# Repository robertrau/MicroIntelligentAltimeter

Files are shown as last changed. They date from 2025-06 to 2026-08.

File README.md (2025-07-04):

# MicroIntelligentAltimeter

The Micro Intelligent Altimeter (Mia) flight computer is not designed as a competition altimeter, but as a model rocket altimeter for young people curious to learn more.
That being said, kids can ask the hardest questions, like, how high did my rocket go, or how fast? So, Mia uses an accurate pressure sensor with a comprehensive software package wrapped around it to provide an accurate altitude.

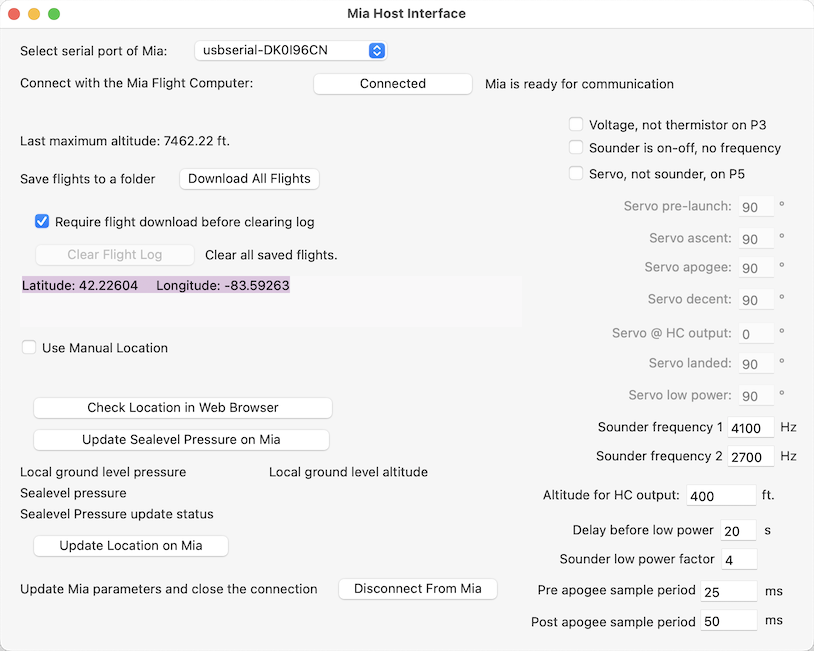
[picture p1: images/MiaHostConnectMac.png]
Picture of Mia's host user interface on a Mac

<p align="center">User Interface on a Mac</p>

<br/><br/>
The board is narrow enough to fit in a BT-5 body tube.

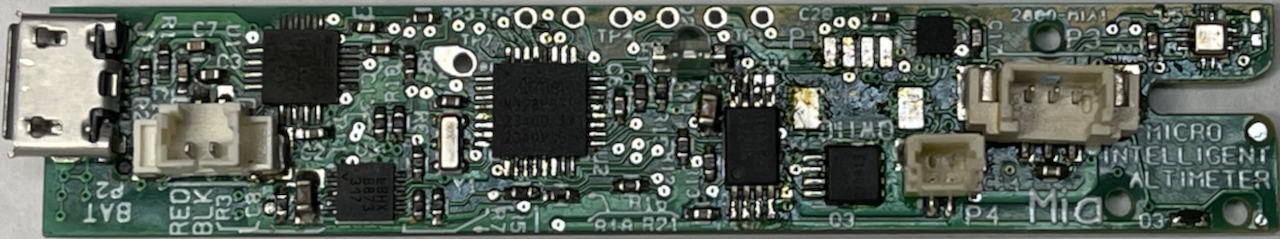
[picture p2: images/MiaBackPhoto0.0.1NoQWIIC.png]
Picture of Mia user interface side

<p align="center">Back of Mia</p>

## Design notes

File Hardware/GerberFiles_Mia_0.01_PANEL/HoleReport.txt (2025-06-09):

Tool   Size   Count  Plated

 T1    0.0550    12     No
 T2    0.0354     6     No
 T3    0.0120   438     Yes
 T4    0.0197     6     Yes
 T5    0.0280    18     Yes
 T6    0.0410     3     Yes

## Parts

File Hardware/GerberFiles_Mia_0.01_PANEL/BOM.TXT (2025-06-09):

1	3	0603-.8x.85	CHG	D2	D2	D2	
2	3	AMPH_10051922-12	OLED	J2	J2	J2	
3	3	ANALOG_DFN10	LTC4063	U3	U3	U3	
4	3	ATMEL_VQFN32	MEGA328	U2	U2	U2	
5	3	BOSCH_BMP390	BMP390	U5	U5	U5	
6	42	C0402R	0.1µF	C1	C11	C12	C13	C14	C15	C17	C18	C19	C2	
					C20	C3	C5	C6	C1	C11	C12	C13	C14	C15	
					C17	C18	C19	C2	C20	C3	C5	C6	C1	C11	
					C12	C13	C14	C15	C17	C18	C19	C2	C20	C3	
					C5	C6	
7	6	C0402R	2.2uF	C10	C9	C10	C9	C10	C9	
8	6	C0402R	33pF	C16	C7	C16	C7	C16	C7	
9	3	C0603R	4.7uF	C4	C4	C4	
10	3	C0805_N	10uF	C8	C8	C8	
11	6	CK_PTS830_S	DISP	SW2	SW4	SW2	SW4	SW2	SW4	
12	3	CK_PTS830_S	RESET	SW3	SW3	SW3	
13	3	CUI_CMT-1102-SMT		PZ1	PZ1	PZ1	
14	6	DFN1006-2	1N4148	D3	D4	D3	D4	D3	D4	
15	3	E_SWITCH_EG1215AA		SW1	SW1	SW1	
16	3	FCI_10118193_S	USB	J1	J1	J1	
17	6	FID40		FID1	FID2	FID1	FID2	FID1	FID2	
18	3	FTDI_WQFN-16	FT230	U1	U1	U1	
19	6	Fiducial_050		U10	U11	U6	U7	U8	U9	
20	3	JST_BM02B	DIGOUT	P4	P4	P4	
21	3	JST_BM04B	QWIIC	P1	P1	P1	
22	3	MEMSIC_12-VFLGA	MC3416	U7	U7	U7	
23	12	MH-NP-0.055		MH1	MH2	MH3	MH4	MH1	MH2	MH3	MH4	MH1	MH2	
					MH3	MH4	
24	3	MOLEX_533984002_S	BAT	P2	P2	P2	
25	3	MOLEX_533984003	ANALOG	P3	P3	P3	
26	3	MOLEX_533984003	EXT BUZ	P5	P5	P5	
27	3	MURATA_CSTNE	8MHz	Y1	Y1	Y1	
28	18	PAD_45.28		TP1	TP2	TP3	TP4	TP5	TP6	TP1	TP2	TP3	TP4	
					TP5	TP6	TP1	TP2	TP3	TP4	TP5	TP6	
29	3	PAD_60.41		TP7	TP7	TP7	
30	3	R0402R	1.00k½	R15	R15	R15	
31	3	R0402R	1.00½	R8	R8	R8	
32	3	R0402R	1.50½	R24	R24	R24	
33	9	R0402R	10.0k½	R14	R17	R6	R14	R17	R6	R14	R17	R6	
34	3	R0402R	100k½	R4	R4	R4	
35	18	R0402R	2.00k½	R12	R13	R16	R22	R23	R9	R12	R13	R16	R22	
					R23	R9	R12	R13	R16	R22	R23	R9	
36	6	R0402R	20.0k½	R18	R5	R18	R5	R18	R5	
37	12	R0402R	21.5k½	R10	R11	R20	R21	R10	R11	R20	R21	R10	R11	
					R20	R21	
38	3	R0402R	274k½	R3	R3	R3	
39	6	R0402R	33.2½	R1	R2	R1	R2	R1	R2	
40	3	R0402R	49.9½	R19	R19	R19	
41	3	R0402_R	0½	R7	R7	R7	
42	3	ROHM_HSMT8	RQ3E180	Q3	Q3	Q3	
43	3	SC-70-6	NL27WZ04	U6	U6	U6	
44	24	TP_CU_50mil		TP10	TP11	TP12	TP13	TP14	TP15	TP8	TP9	TP10	TP11	
					TP12	TP13	TP14	TP15	TP8	TP9	TP10	TP11	TP12	TP13	
					TP14	TP15	TP8	TP9	
45	3	TSSOP-8	CAV24M01	U4	U4	U4	
46	438	VIA-OsmLib		VIA1	VIA100	VIA101	VIA102	VIA103	VIA104	VIA105	VIA106	VIA107	VIA108	
					VIA109	VIA11	VIA110	VIA111	VIA112	VIA113	VIA114	VIA115	VIA116	VIA117	
					VIA118	VIA119	VIA12	VIA120	VIA121	VIA122	VIA123	VIA124	VIA125	VIA126	
					VIA127	VIA128	VIA129	VIA13	VIA130	VIA131	VIA132	VIA133	VIA134	VIA135	
					VIA136	VIA137	VIA138	VIA139	VIA14	VIA140	VIA141	VIA142	VIA143	VIA144	
					VIA145	VIA146	VIA147	VIA148	VIA15	VIA16	VIA17	VIA18	VIA19	VIA2	
					VIA20	VIA21	VIA22	VIA23	VIA24	VIA25	VIA26	VIA27	VIA28	VIA29	
					VIA3	VIA30	VIA32	VIA33	VIA34	VIA35	VIA36	VIA37	VIA38	VIA39	
					VIA4	VIA40	VIA41	VIA42	VIA43	VIA44	VIA45	VIA46	VIA47	VIA48	
					VIA49	VIA5	VIA50	VIA51	VIA52	VIA53	VIA54	VIA55	VIA56	VIA57	
					VIA58	VIA59	VIA6	VIA60	VIA61	VIA62	VIA63	VIA64	VIA65	VIA66	
					VIA67	VIA68	VIA69	VIA7	VIA70	VIA71	VIA72	VIA73	VIA74	VIA75	
					VIA76	VIA77	VIA78	VIA79	VIA8	VIA80	VIA81	VIA82	VIA83	VIA84	
					VIA85	VIA86	VIA87	VIA88	VIA89	VIA9	VIA90	VIA91	VIA92	VIA93	
					VIA94	VIA95	VIA96	VIA97	VIA98	VIA99	VIA1	VIA100	VIA101	VIA102	
					VIA103	VIA104	VIA105	VIA106	VIA107	VIA108	VIA109	VIA11	VIA110	VIA111	
					VIA112	VIA113	VIA114	VIA115	VIA116	VIA117	VIA118	VIA119	VIA12	VIA120	
					VIA121	VIA122	VIA123	VIA124	VIA125	VIA126	VIA127	VIA128	VIA129	VIA13	
					VIA130	VIA131	VIA132	VIA133	VIA134	VIA135	VIA136	VIA137	VIA138	VIA139	
					VIA14	VIA140	VIA141	VIA142	VIA143	VIA144	VIA145	VIA146	VIA147	VIA148	
					VIA15	VIA16	VIA17	VIA18	VIA19	VIA2	VIA20	VIA21	VIA22	VIA23	
					VIA24	VIA25	VIA26	VIA27	VIA28	VIA29	VIA3	VIA30	VIA32	VIA33	
					VIA34	VIA35	VIA36	VIA37	VIA38	VIA39	VIA4	VIA40	VIA41	VIA42	
					VIA43	VIA44	VIA45	VIA46	VIA47	VIA48	VIA49	VIA5	VIA50	VIA51	
					VIA52	VIA53	VIA54	VIA55	VIA56	VIA57	VIA58	VIA59	VIA6	VIA60	
					VIA61	VIA62	VIA63	VIA64	VIA65	VIA66	VIA67	VIA68	VIA69	VIA7	
					VIA70	VIA71	VIA72	VIA73	VIA74	VIA75	VIA76	VIA77	VIA78	VIA79	
					VIA8	VIA80	VIA81	VIA82	VIA83	VIA84	VIA85	VIA86	VIA87	VIA88	
					VIA89	VIA9	VIA90	VIA91	VIA92	VIA93	VIA94	VIA95	VIA96	VIA97	
					VIA98	VIA99	VIA1	VIA100	VIA101	VIA102	VIA103	VIA104	VIA105	VIA106	
					VIA107	VIA108	VIA109	VIA11	VIA110	VIA111	VIA112	VIA113	VIA114	VIA115	
					VIA116	VIA117	VIA118	VIA119	VIA12	VIA120	VIA121	VIA122	VIA123	VIA124	
					VIA125	VIA126	VIA127	VIA128	VIA129	VIA13	VIA130	VIA131	VIA132	VIA133	
					VIA134	VIA135	VIA136	VIA137	VIA138	VIA139	VIA14	VIA140	VIA141	VIA142	
					VIA143	VIA144	VIA145	VIA146	VIA147	VIA148	VIA15	VIA16	VIA17	VIA18	
					VIA19	VIA2	VIA20	VIA21	VIA22	VIA23	VIA24	VIA25	VIA26	VIA27	
					VIA28	VIA29	VIA3	VIA30	VIA32	VIA33	VIA34	VIA35	VIA36	VIA37	
					VIA38	VIA39	VIA4	VIA40	VIA41	VIA42	VIA43	VIA44	VIA45	VIA46	
					VIA47	VIA48	VIA49	VIA5	VIA50	VIA51	VIA52	VIA53	VIA54	VIA55	
					VIA56	VIA57	VIA58	VIA59	VIA6	VIA60	VIA61	VIA62	VIA63	VIA64	
					VIA65	VIA66	VIA67	VIA68	VIA69	VIA7	VIA70	VIA71	VIA72	VIA73	
					VIA74	VIA75	VIA76	VIA77	VIA78	VIA79	VIA8	VIA80	VIA81	VIA82	
					VIA83	VIA84	VIA85	VIA86	VIA87	VIA88	VIA89	VIA9	VIA90	VIA91	
					VIA92	VIA93	VIA94	VIA95	VIA96	VIA97	VIA98	VIA99	
47	3	VISHAY_VEMT2	VEMT2523SLX01	Q2	Q2	Q2

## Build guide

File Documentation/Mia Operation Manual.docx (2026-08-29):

Mia

Micro Intelligent Altimeter

A Rocket Sensor Platform for Learning

Arduino Compatible

Pressure Altimeter

Thermometer

Accelerometer

Revision 0.06

7/23/2025

Read this entire manual

Introduction

Congratulations, you have just ~~purchased~~, er, bought the parts, soldered, loaded a bootloader, and programmed a Mia flight computer!

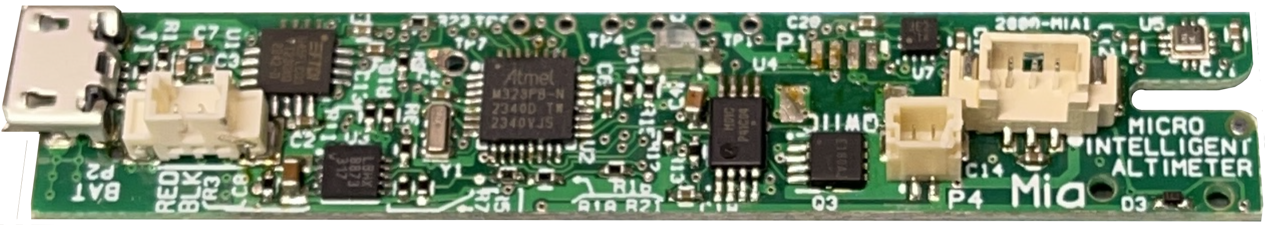
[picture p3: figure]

The Mia flight computer is not designed as a competition altimeter, but as a model rocket altimeter for young people curious to learn more.

That being said, kids can ask the hardest questions, like, how high did my rocket go, or how fast? So, Mia uses an accurate pressure sensor with a comprehensive software package wrapped around it to provide an accurate altitude when needed. You can review the accuracy specifications in the BMP581 data sheet.

In its simplest form, you can turn on your Mia, pop it into a rocket, launch, and recover it, and read your peak altitude on the OLED display. Then do it all over again. No mobile device or computer required. A tiny 30mAh LiPo cell with last for hours of flying. Without worrying about setting the sea level pressure, your reported altitudes may be a little shifted, but they will be accurate relative to one another. You can count on the Mia to find the winner in a friendly altitude competition.

If you require an accurate altitude, using only the buttons and OLED display, you can set the sea level pressure or field altitude for your location. This will likely require a mobile device to retrieve this data from a weather site, GPS, or mobile application. If you have a Windows/Mac/Linux/Raspberry Pi computer with internet access, you can use the Mia host application to set sea level, as well as other features. With an accurate sea level pressure set your reported altitude will be very accurate. See Appendix A for details on how an accurate sea level pressure, or field altitude, is required to provide an accurate altitude.

More advanced flyers, using the host computer application, with internet access, can do:

1. Set sea level pressure (automatic with internet connection and nearby national weather service measurement)
2. Set time (automatic with internet connection)
3. Location (automatic with internet connection)
4. Downloading and clearing of flight log data
5. Set the altitude for the high current output to turn on during descent.
6. Configure low power options
7. Configure Mia for what is connected to connector P3 (thermistor, or a sensor with voltage output)
8. Configure Mia for what is connected to connector P5 (sounder or servo)

Then the Mia can be flown, and after recovery, a flight log can be downloaded with the host application and the flight log can be viewed in a spread sheet. If the user prefers to use a terminal emulator, all parameters and downloads can be performed with the command interface.

For those with an interest in programming, all the flight firmware and host computer software are available as open-source software. The flight firmware is developed in the free Arduino IDE. The code is heavily commented to help those wanting to change, experiment, or just learn from the code. The host application is developed in the low cost XOJO IDE (free for targeting only the Raspberry Pi).

Description

The Mia is a small formfactor sensor platform with embedded software designed for young people interested in rockets, science, technology, engineering, or who are just looking for a challenge.

The Mia includes:

1. An Arduino based architecture providing an accessible and well supported development environment.
2. A power supply that allows operation from a battery, or USB power with a battery attached.
3. USB to serial bridge for communicating with the MCU with the Arduino environment
4. An OLED display as a user interface
5. Three buttons as part of the user interface.
6. Pressure sensor for altitude.
7. A three-axis accelerometer.
8. Light sensor.
9. A connector, P3, that can monitor an external thermistor or any other voltage-output sensor
10. A high current output that switches to ground.
11. QWIIC connector for sensor expansion.
12. Either a soldered-on sounder or a connector, P5, for either a sounder or servo.
13. A 2-megabit flight log EEPROM. This stores 8 thousand flight records.
14. The MCU is a Microchip ATMEGA328PB with 32kB of FLASH memory running at 8MHz.

The flight firmware includes:

1. Flight mode displays maximum altitude after rockets lands.
2. Accurate altitude settings can be entered without a mobile device or computer.
3. Can set sea level/field altitude
4. Can set altitude for high current output to trigger

Basic Operation

For the most simple and fun applications, the Mia offers modest accuracy maximum altitude (apogee) reporting without any other equipment. For reliable and long-lasting performance, some care and preparation are required.

1. The Mia can be damaged by rocket motor ejection charge gases. The Mia must be used in a payload section of a rocket and never put in with the parachute or streamer. Also check that your payload barrier between the payload section and the parachute compartment is airtight. Some plastic adapters have openings where ejection gases can pass into the payload section.
2. The Mia battery must be supported so the wires can’t be stressed during launch or ejection. It is a good idea to use double sticky foam tape to mount the battery to the Mia.
3. If your Mia is built without certain parts and flown as a bare PCB assembly, your Mia can fit in a body tube as small as a BT-5. The battery must be below the Mia in this small of a body tube. Make sure that the battery wires will not be stressed. See Appendix C for build requirements for BT-5 applications.
4. Remember to make it easy to get your Mia out of its payload section so you can read the maximum altitude.
5. Many payload sections are simply friction fit together. Even though the Mia weights about 5 grams, during ejection it can overcome the friction holding a payload section together and fall out hundreds of feet in the air. Use tape to hold a payload section together so you don’t lose your Mia.
6. Using a pressure sensor to measure altitude requires your payload to be at the pressure around your rocket. You must have a small hole from your payload section to the outside to get an accurate altitude. Do not put the hole in your nose cone or you will get an incorrect pressure.
7. After you have installed you Mia in its payload section it is a good idea to use an easy-to-remove tape (such as blue painter’s tape) over the air hole so wind blowing over the hole won’t trigger a launch detect.
8. If you want to use the light sensor as a spin rate sensor you must have a hole in your payload section or a clear payload section for the light to enter. This hole can also serve as the air pressure entry if the hole location is located far enough back for a real pressure reading.

Intermediate Operation

For applications where you want accurate altitude and to use the high current output, you can use the buttons and display on the Mia. No host computer is needed but you will need to set the sea level pressure to get an accurate altitude.

Advanced Operation

For applications where you want to change how the Mia behaves you can use the Mia Host application. It runs on Windows, Mac, x86 Linux, and the Raspberry Pi.

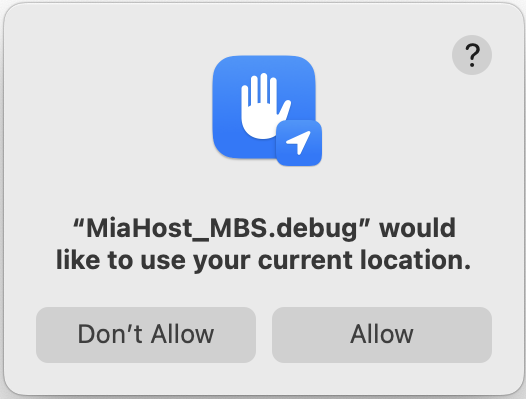
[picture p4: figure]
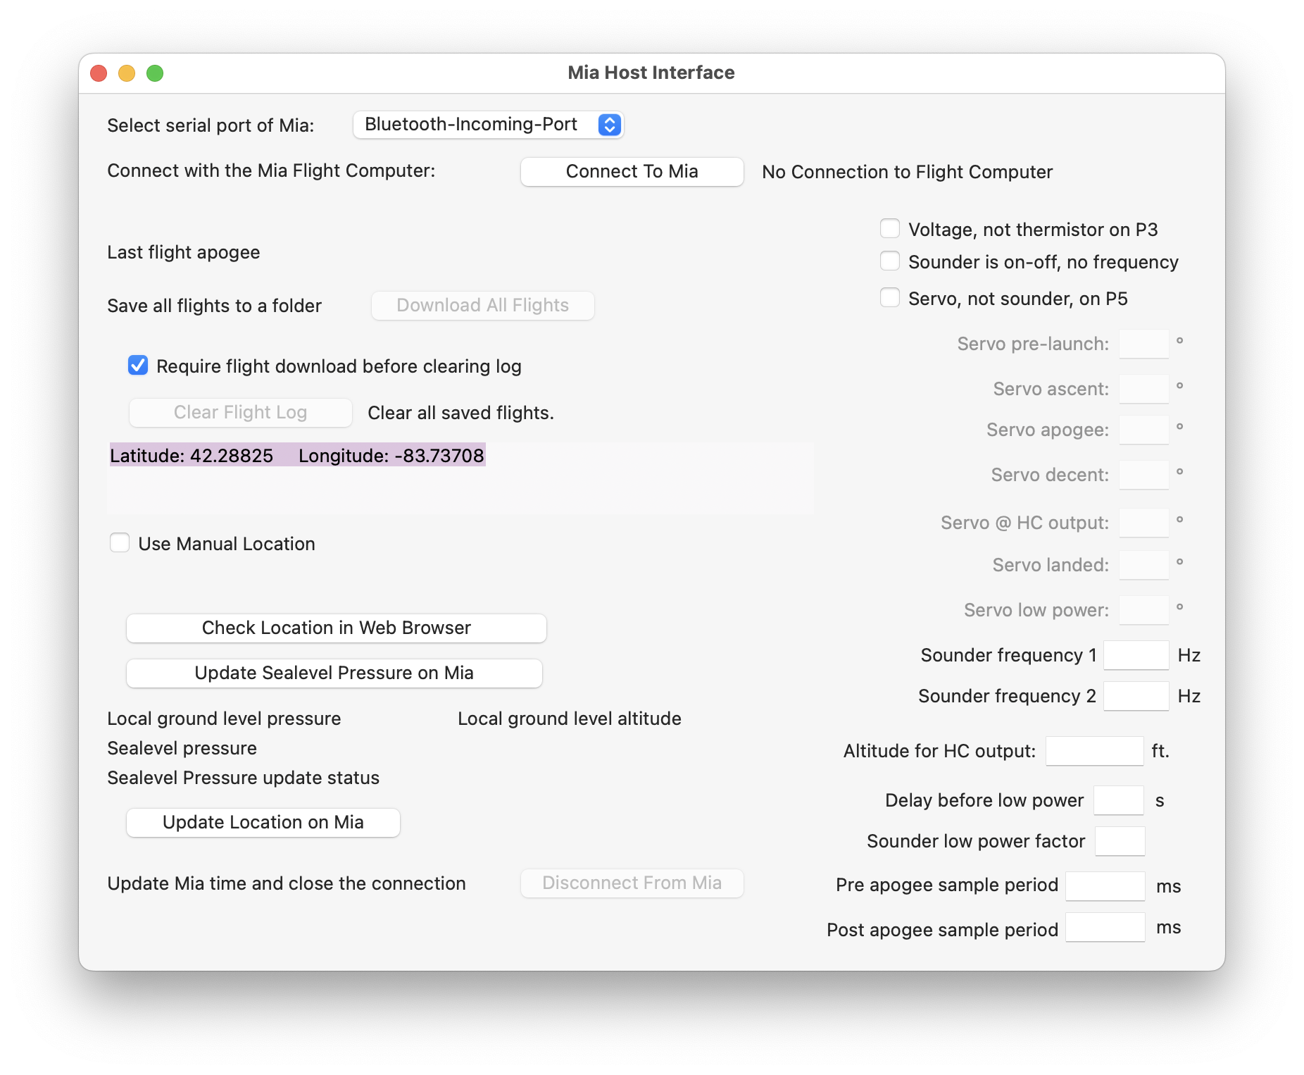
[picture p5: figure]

The left side of the Mia Host window is where you establish your connection with your Mia, download your flight logs, update your sea level pressure, location, and time.

The right side of the Mia Host window allows some advanced user configuration features.

Most of these features requires external hardware connections to the Mia. The options for low power operation do not require any additional connections or hardware.

Voltage, not thermistor on P3

The user can plug a muRata NXFT15XH103FEAB050 thermistor into P3, or any other voltage output sensor. If the thermistor is used the Mia does the conversion from resistance to temperature. If another sensor is used, the Mia will record the voltage on P3. Check the box if you are using a voltage output sensor.

Sounder is on-off, no frequency

Servo Pre-launch

The servo position while waiting for lift off. Set to a value from 0 to 180.

Servo Ascent

The servo will move to this position at launch detect. It will stay at this position through the ascent. Set to a value from 0 to 180.

Servo Apogee

At apogee the servo will move tto this position. Then, after 0.40 seconds, the servo will move to the descent position. Set to a value from 0 to 180.

Servo Descent

The servo will move to the descent position after the 0.40 second long Apogee position. It will stay at this position until the altitude set for the high current output. Then it moves to the 'Servo @ HC output' position. Set to a value from 0 to 180.

Servo @ HC Output

The servo will move to this position at the altitude set for the high current output to turn on. It will stay at this position through landing. Set to a value from 0 to 180.

Servo Landed

After detecting landing the servo moves to this position. It stays here for the duration of the 'Delay before low power' timer, then the servo will move to its last position, the low power position. Set to a value from 0 to 180.

Servo Low-Power

After the flight is complete and the delay before low power time has passed the servo moves to this final position. Set to a value from 0 to 180.

Altitude for high current output

Set the altitude that this output turns on during descent.

The high current output on connector P4 can sink up to 1 amp of current if wired with 28AWG wiring. The MOSFET switch to ground is a high current device with a ‘on’ resistance of 6 milliohms. The connector is rated at 1.0 amp so only use low current devices.

Programming the Mia for custom requirements

The source code is well commented with hundreds of lines of details and explanation. There are also notes specifically for programmers and software engineers who want to modify the Mia software.

If you are a developer, here is some helpful information

Source code conventions:

We use the prefix N_ for active low digital pins.

Part way through the project we started adding a units suffix to variables to reduce unit confusion.

Unused MCU pins must be either an output or an input with a pull up or down so the pins don't float and draw excess current.

Programmer tips:

1) This software keeps track of approximate date and time. This helps keep flight logs in order. Please keep the #define BIRTH_TIME_OF_THIS_VERSION up to date with every build.

2) If you are adding software to Mia and need more FLASH space, you can:

A) Reduce or eliminate the instructions in DisplayInstructions() function. (Just comment out the call 'DisplayInstructions();', the linker will dead strip.)

B) Reduce or eliminate DoSplashScreen() function.

C) Reduce or eliminate DoSensorDisplayLoop() function as this is only used for diagnostics.

D) Reduce or eliminate the temperature look up table (about 412 bytes) and convert temperature differently, or not at all.

E) Remove auto-configuration support for the old Mia 0.0.0

F) Remove Buzzer function if not used.

G) Remove servo support if not used.

H) Revert to the standard ATMEGA328 Variant. You loose access to D23-D26 which may not matter but this saves a few hundred bytes.

I) Remove the host mode help command.

J) If a buzzer on-off pattern is not required, you can eliminate the DoBuzzer() function.

3) Internaal EEPROM addresses 232 and up are unused.

4) Test Point 7 has a hole on the board large enough to easily solder to, it is connected to D3. It is currently unused and available for any purpose.

5) Many different sensors, Memory, controllers are available with a QWIIC connector that can be used with the Mia.

Appendix A

Details of using air pressure to find altitude.

Air pressure is a good indication of altitude and has been used for that purpose for aircraft from 1928 to the present. That being said, it is not an absolute solution, it still needs a reference pressure. Aircraft altimeters allow you to dial in a pressure with a knob on the side of the dial. This is an important step in the pre-flight checklist for any aircraft pilot. This step is also an important step for you with the Mia.

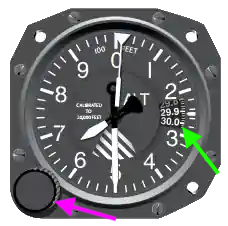
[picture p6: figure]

Figure 2345

To understand what is going on with air pressure you need to understand that air is compressible. As a comparison, water is not compressible. This makes the math very different for finding your depth in water verses finding your height in the air.

Imagin you are 100 feet under water and you want to rise to 50 feet under water. This is similar to a stack of 100 glass marbles in a tube. Half the pressure will be half the marbles, and half the marbles will be 50 feet up, easy.

Now, lets say you are on the surface of the land and you want to go up 50 feet. This time we are in compressible air. Imagine now that you have a tube filled with soft foam balls instead of marbles. At the top your balls are still round, but at the bottom you have a squished nearly flat foam ball from the weight of the other balls. This time you count up 50 foam balls and you are no where near half way.

This is further complicated by the fact that just like the ocean has waves, our atmosphere has waves, we call them high pressure regions.

More can be learned at these links:

https://www.engineeringtoolbox.com/air-altitude-pressure-d_462.html

https://en.wikipedia.org/wiki/Atmospheric_pressure

Earth’s daily pressure changes:

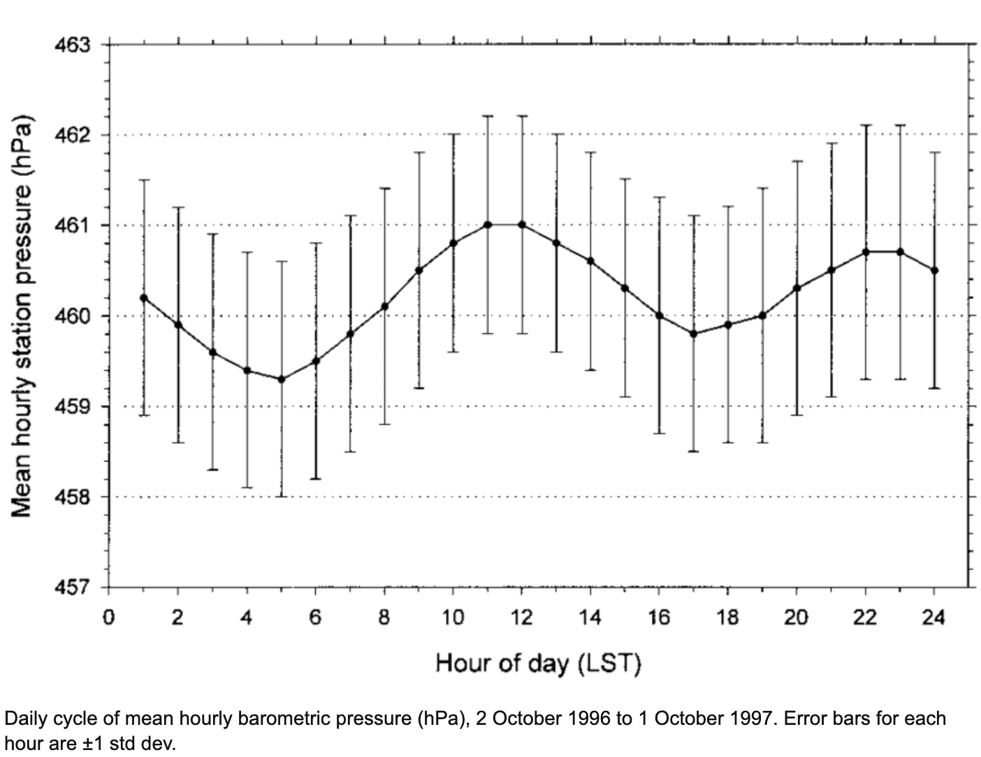
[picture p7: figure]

Here is a collection of high and low pressure extremes on earth on May 13, 2026.

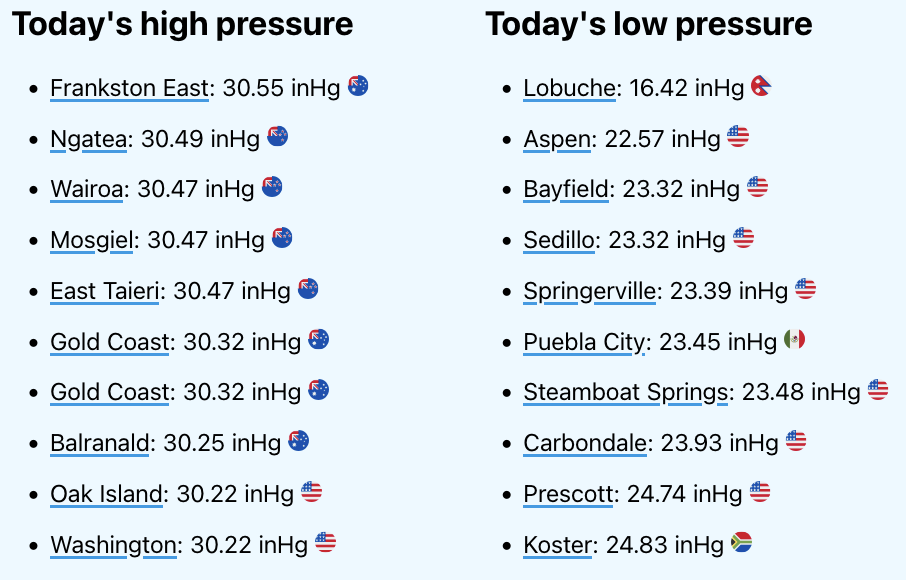
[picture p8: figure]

An example of reported altitudes with and without sea level pressure correction.

For a city with an elevation of 191 meters, Ypsilanti, MI

For a day with a pressure of 15.0 mb below normal

Using uncertainty of a BMP581 sensor,

Apogee altitude above sea level with sea level correction is between 1640.85 meters, and 1641.15 meters.

Apogee altitude above sea level without sea level correction is between 1761.82 meters, and 1762.12 meters.

With sea level correction altitude will be reported between 1449.85 and 1450.15

Without sea level correction altitude will be reported between 1445.74 and 1446.04

Appendix B

Example science projects using the Mia

Compare altitude measure methods by integrating acceleration vs. air pressure.

Upper atmospheric air sample mission using a servo.

Rocket spin rate and its effect on maximum altitude using the light sensor and different fin angles.

The effect of microgravity on light interfering solutions using the light sensor and accelerometer.

Appendix C

Requirements and recommendations for using the Mia in BT-5 body tubes.

The Mia PCB is 12.8mm wide. By itself this easily fits in a BT-5. If the Mia is assembled with optional certain components, it will not fit in a BT-5. These are detailed below:

1. Connector P5 must not be installed, or it will directly interfere with a BT-5
2. Connector P1 must not be used. P1 doesn’t interfere with a BT-5 but the mating connector will interfere with a BT-5
3. The OLED display must be attached with 1.5mm thick double sided foam tape. Any thicker and the OLED will interfere with a BT-5
4. The battery will not fit along side of the Mia, it must be place above or below the Mia. The Mia and battery must be mounted so the battery wires are not stressed.
5. BT-5 diameter rockets limit you to small rocket motors. This may make you want to remove all the unnecessary mass you can. The Mia will operate as an altimeter without the following components:

Connectors: P1, P3, P4, and P5. Other components: Q2 (light sensor), Q3 (High current sensor).

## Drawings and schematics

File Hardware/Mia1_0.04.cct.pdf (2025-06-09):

A | A
B | B
C | C
D | D
E | E
F | F
G | G
H | H
I | I Date:
Document Number: | Rev:

## Sheet:

## TITLE:

Rev. 0.00 Prototype release
Rev. 0.01 Added SW4 and CHG signal to MCU inputs. Added series resistors on TX & RX lines between LTC4063 & FT230 power domains.
Added accelerometer. Changed battery charge resistor values. Added capacitance on Plus3.0V. Board narrowed by 0.2mm. Added USB ESD capacitors.
Rev. 0.02 Layout improvment. PCB part number added as "MIA1-0.02"
Rev. 0.03 Layout improvment around accelerometer, improved grounding. PCB PN reduced to version only "0.03"
Rev. 0.04 Changed BMP390 to a BMP581. Changed U4 to a 2Mb ST M24M02E. No layout change.

PCB Assembly mass: &GmMassTot grams

Copyright 2024-2025, all rights reserved

Design Revision: 0.01 | Drawing Revision: H

PCB Fabrication Notes:
1) Each board in the panel must have a unique number, in
copper, to track which part of the panel each board came from.
2) The solder mask must be green.
3) Solder side silkscreen must be must.
4) Component side silkscreen must be white.

Component Hole Count: 8

# FINISHED

SMT pad Count: 496

Board width: 12.8 mm

Board length: 65.5 mm
Modified: 5/9/25 5:07 PM

Created: 4/21/25 8:46 PM

## Small Rocket Computer

File: Mia1_0.04.cct | 2000-MIA1-0.01

Printed: 5/9/25 5:07 PM

Component side area used is 456 mm^2, or 53% of 851.5 mm^2

Cost of Assembly: &CostTotalAsy

Warning Count: 74

Operating temperature range: 0° C to 70°C &NoteTempWavr

Error Count: 0

Package count solder side: 23

Package count component side: 53

Net List File Name: Mia1_0.04.txt

At a quantity of: 10

Parts Cost: $40.1189

Designer: Robert & Rich Rau

Solder side area used is 490 mm^2, or 57% of 851.5 mm^2

Custom attributes:

fill in different build attributes

Last Used Devices:
C20
D4
FID2
HW1
J2
MH4
P5
PCB7
PZ1
Q3
R24
SW4
TP15
U7

PCB Layout Notes:
1) Test points accessable from bottom.
2) OLED & switches on same side of board.
3) Add vias on SMT connector machanical pads.

# 2000-MIA1-0.01

Attach OLED to J2

Bottom side SMT

Assembly Step 3

Assembly Step 2

Assembly Step 1

Top side SMT

Unused Units:

Top Side Documentation | Bottom Side Documentation

Silkscreen: Mia

FID1

Fiducial,40mil,Top/Bot side

FID2

Fiducial,40mil,Top/Bot side

Printed Circuit Board:
In Copper:

Printed circuit board, FR4, 1.0mm thick, 2 Layer

1700-MIA1-0.03

PCB NOTE:
All nets that start with KS are "Keep Short" nets. They are grouped at the top of the netlist. PCB5

PCB NOTE:
All connector silkscreen RefDes must be 3mm high on both sides of the board where possible. PCB6

MH1

MH-NP-0.055

MH2

Silkscreen: | MICRO INTELLIGENT ALTIMETER
Silkscreen: | BOARD: PRO MINI
Silkscreen: | PROC: ATMEGA328P 3.3V
MH3 | MH4

B | B
2000-MIA1-0.01 | FINISHED

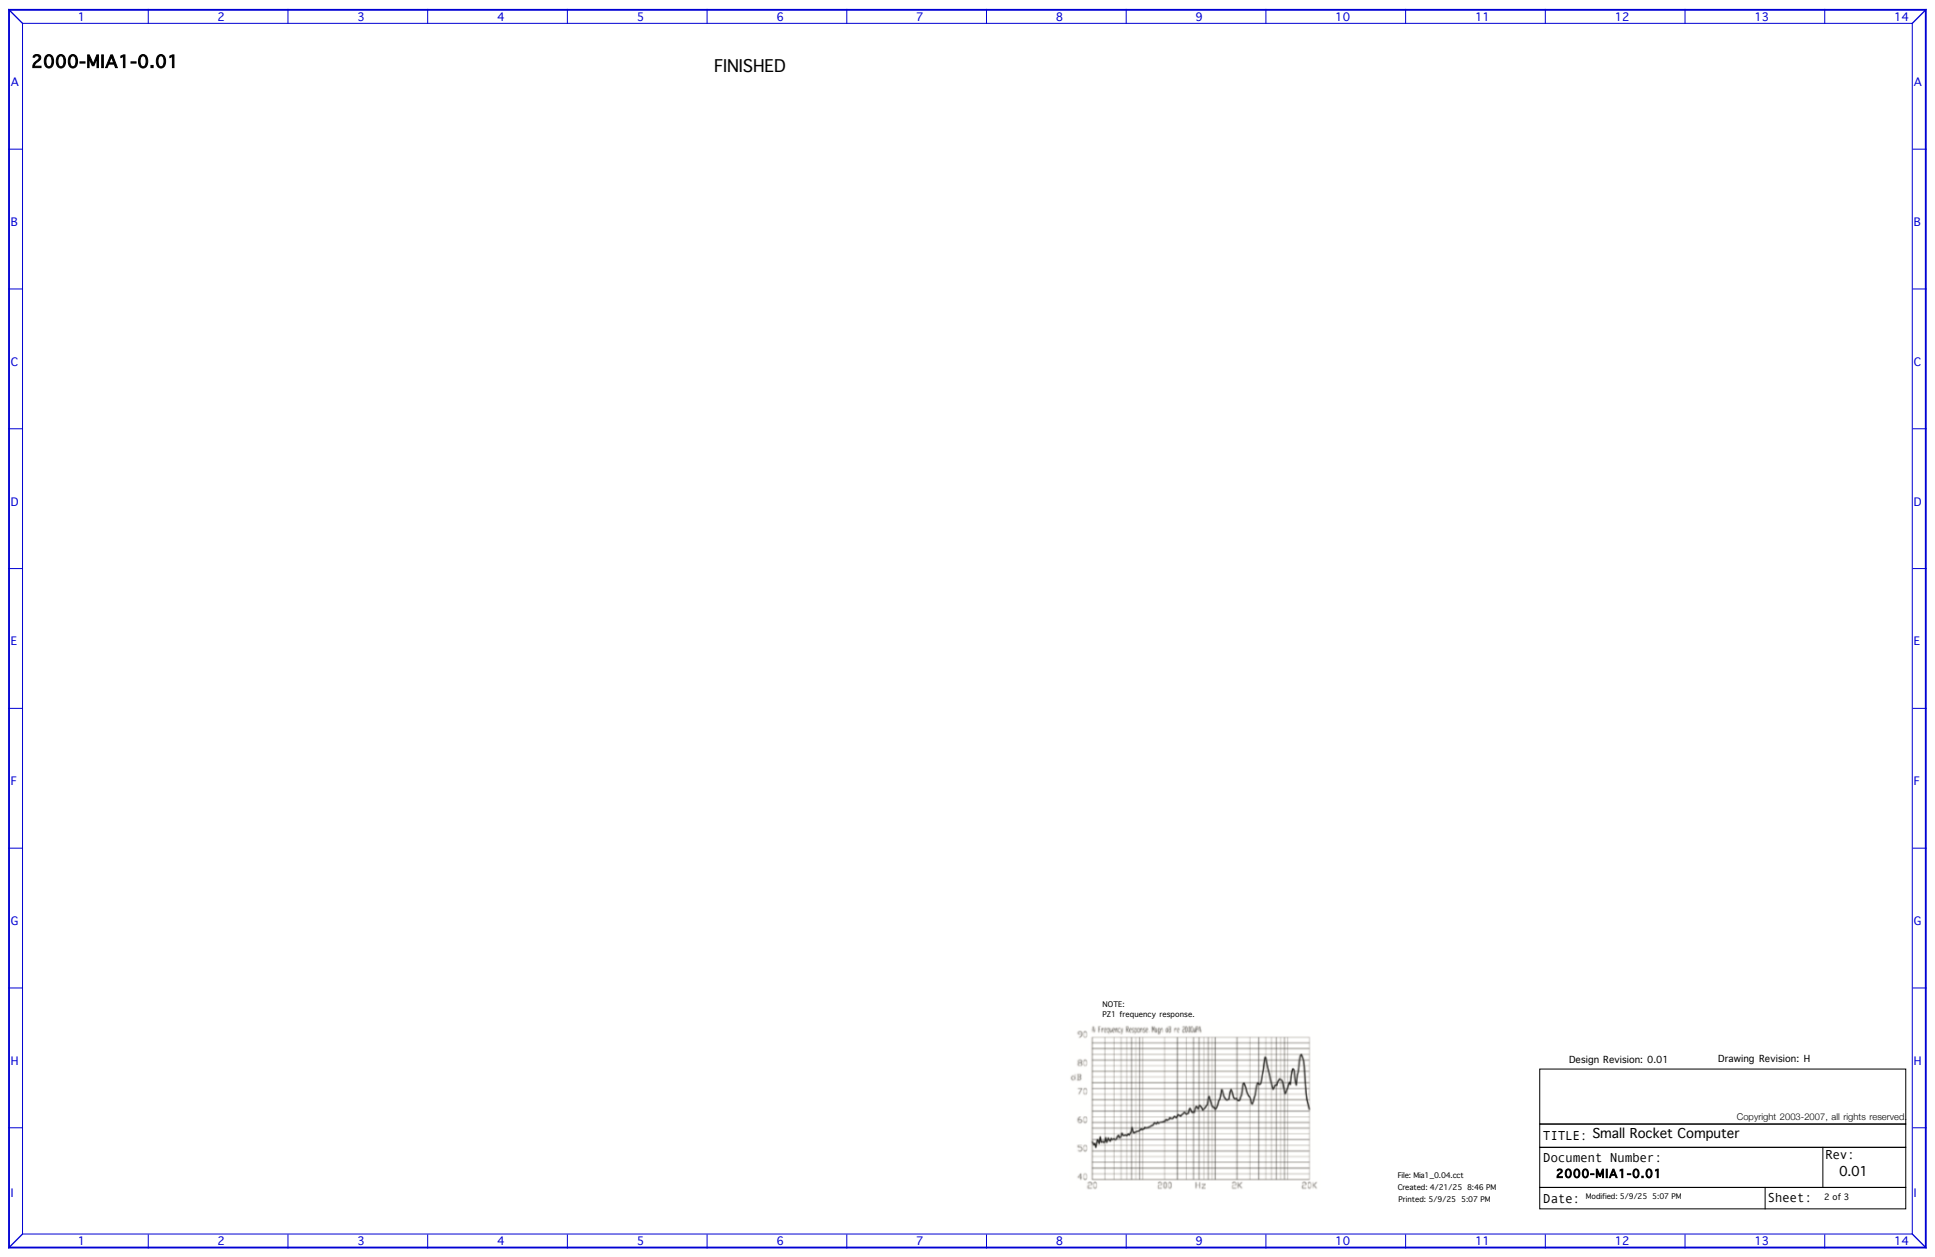
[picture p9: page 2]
I Date:; Document Number:; Rev:; TITLE:; NOTE: PZ1 frequency response.; Design Revision: 0.01; Drawing Revision: H; File: Mia1_0.04.cct; 2000-MIA1-0.01

Copyright 2003-2007, all rights reserved.

Small Rocket Computer

B | B

# FINISHED

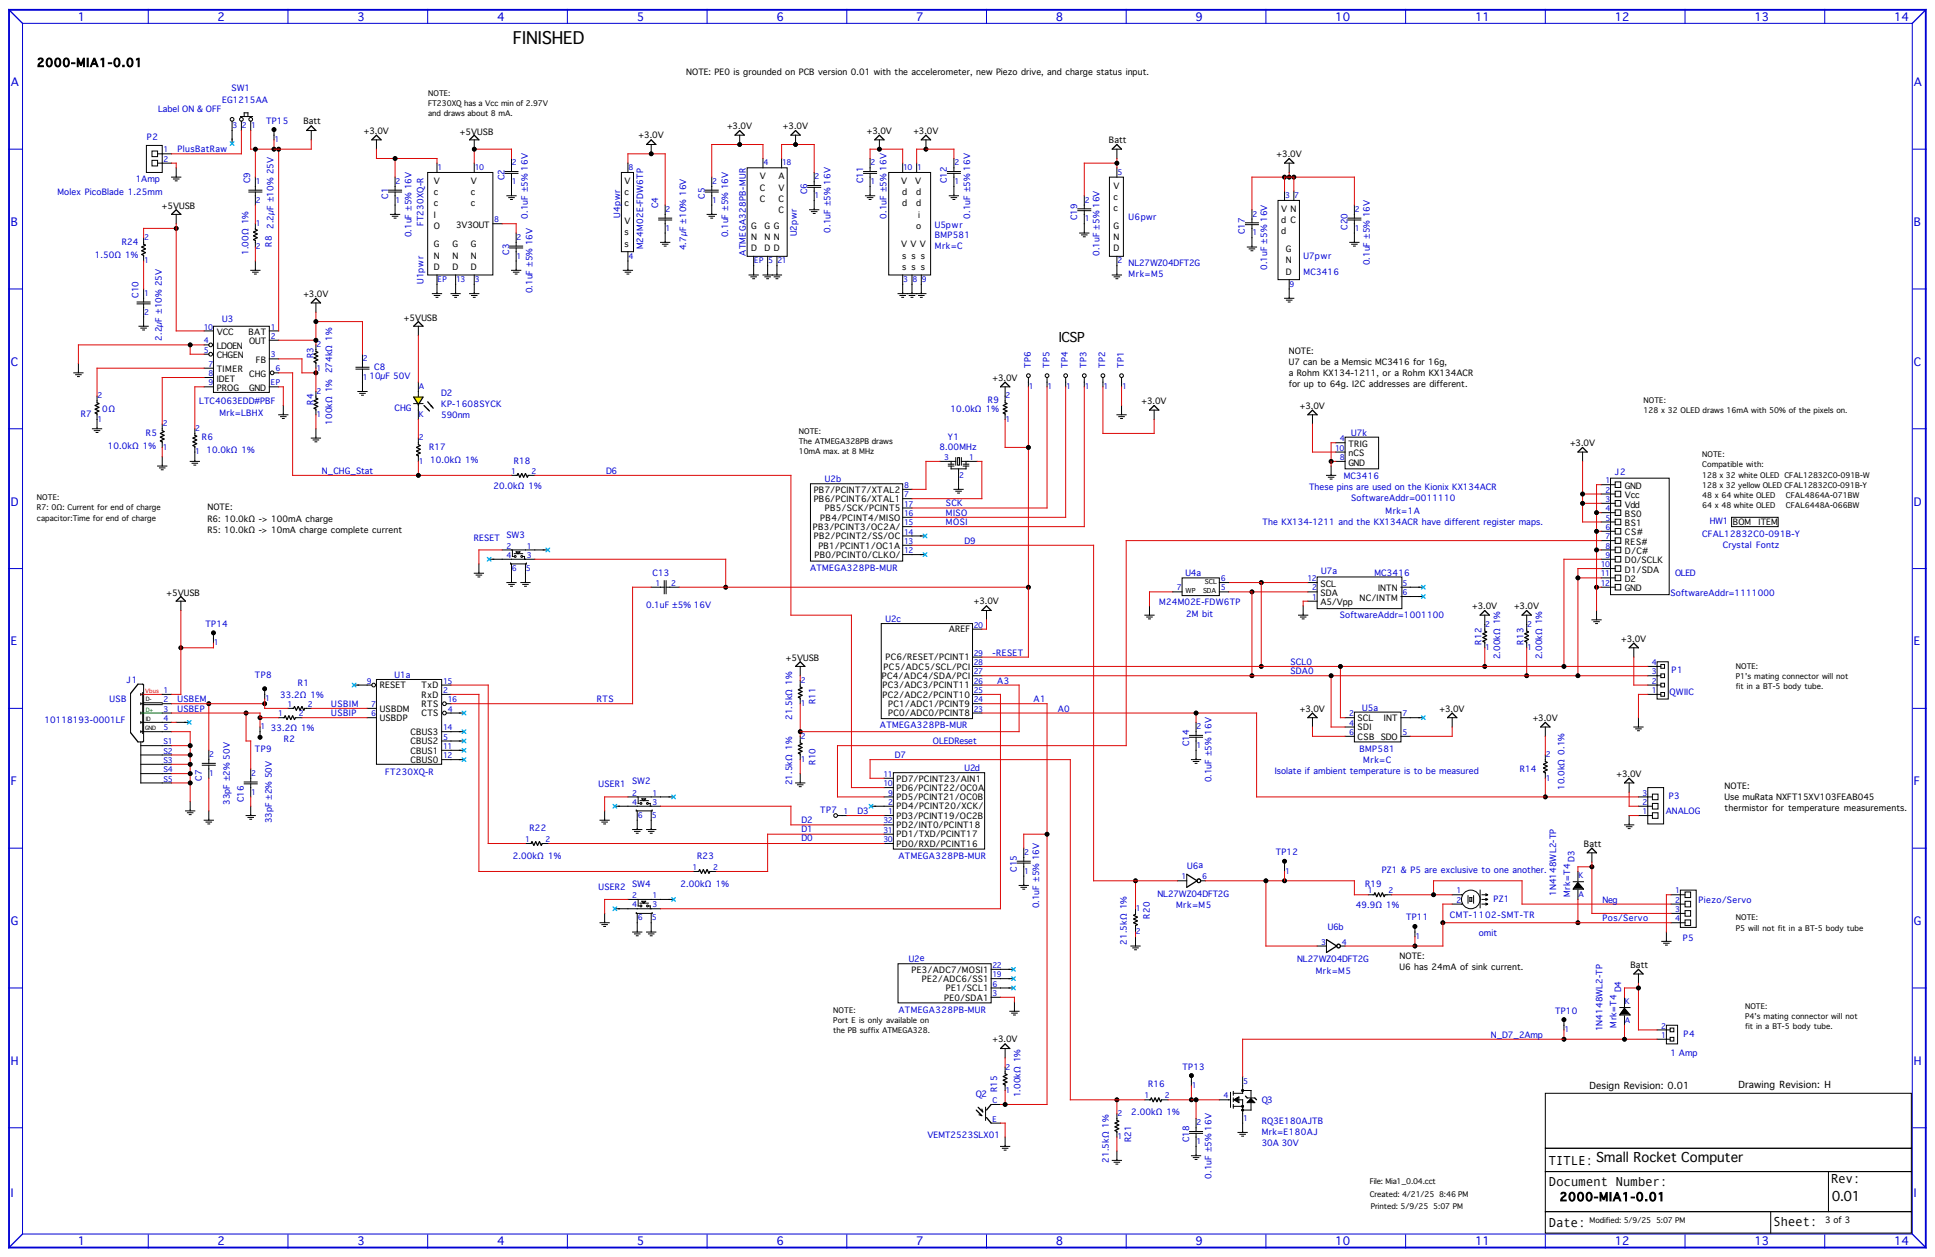
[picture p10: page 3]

NOTE: PE0 is grounded on PCB version 0.01 with the accelerometer, new Piezo drive, and charge status input.

NOTE:
FT230XQ has a Vcc min of 2.97V
and draws about 8 mA.

U7 can be a Memsic MC3416 for 16g,
a Rohm KX134-1211, or a Rohm KX134ACR
for up to 64g. I2C addresses are different.

128 x 32 OLED draws 16mA with 50% of the pixels on.

These pins are used on the Kionix KX134ACR

R7: 0Ω: Current for end of charge
capacitor:Time for end of charge

The KX134-1211 and the KX134ACR have different register maps.

P1's mating connector will not
fit in a BT-5 body tube.

Isolate if ambient temperature is to be measured

Use muRata NXFT15XV103FEAB045
thermistor for temperature measurements.

P5 will not fit in a BT-5 body tube

Port E is only available on
the PB suffix ATMEGA328.

P4's mating connector will not

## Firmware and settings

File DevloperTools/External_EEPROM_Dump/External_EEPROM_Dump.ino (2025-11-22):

#define STRINGIFY(s) XSTRINGIFY(s)
#define XSTRINGIFY(s) #s  // So you can do #pragma message ("Compile_Time_Var= " STRINGIFY(Compile_Time_Var)) and see it in the compilier messages

#include <Arduino.h>
#include <Wire.h>
#include <Servo.h>
#include <EEPROM.h>  // Arduino on chip EEPROM (1k byte)  Used for date, time, setup parameters, more, see below.

/**
    @file   Rocket_Altitude_4_6.ino

    @brief  Firmware for the Mia, version 0.0.0 and 0.0.1, Micro Integellient Altimeter, rocket flight computer. Using the BMP581 pressure sensor and ST M24M02E EEPROM.

    @details Micro Integellient Altimete (Mia) is a rocket flight computer with several sensors, serial port interface, and EEPROM data logging.
             Mia was designed for young kids to answer the question "How high did my rocket go?" Mia answers this question with a pressure sensor and a temperature sensor.
             Less than 13mm wide, Mia fits into body tubes as small as BT-5, allowing very small and inexpensive rockets to fly Mia. As Mia evolved, a light sensor, Logging EEPROM,
             an accelerometer, expansion connector, and improved user interface was added. Mia stayed the same dimensions with these additions.
             Beyond just answering that important question "How high did my rocket go?" Mia can help older kids with STEM/STEAM projects or science fair projects.
             The light sensor provides roll rate data, Temperature, as well as improving altitude data can show the lapse rate of temperature with altitude.

             Mia was designed to help young kids stay interested in rocketry from a STEM/STEAM perspective. Flight data is logged allowing rich data for science fair projects.
             Expansion is available through a analog input connector and a QWICC connector. All firmware is open source under the MIT license. Anybody is free to ues this code
             anyway they want, without requirements of giving back, although we would love you to share your additions! :-)
             This firmware uses the BMP581 altimeter, a Vishay VEMT2523SLX01 as a light sensor for possible roll data, a muRata NXFT15XH103FEAB050 thermistor on connector P3 to
             log flight data. Then the OLED will report maximum altitude above ground level in feet.
             The 0.0.1 version adds a I2C KX134ACR accelerometer, charge status to Arduino digital input 6, and a second user button.

             Mia is supported with a host program for Windows, MacOS, Linux, and Raspberry Pi. The host program can:
              Download flight logs
              Clear the log
              Lookup your latitude and longitude and set it in the Mia
              Find the sealevel pressure from NMS over the web and set it
              Set the date
              Read the last maximum altitude
              Setup servo or buzzer feature
              Setup servo settings

*/
// Mia Block Diagram
//                                                            ┌───────────────────────┐
//                                        ┌──────────┐        │ ICSP Test Points for  │
//                                      ┌─┤ 8.00MHz  ├─┐      │programming bootloader │
// ┌────┐                               │ └──────────┘ │      └──────────┳────────────┘
// │    │   ┌──────────┐   Reset     ┌──┴──────────────┴─┐               ┃
// │    │   │          ├────────────▶│                   │◀━━━━━━━━━━━━━━┛
// │    │◀━▶│ FT230XQ  │             │                   │           ┌─────────────────┐
// │    │   │          │   Serial    │                   │◀──────────┤  Light Sensor   │
// │    │   │          │◀━━━━━━━━━━━▶│                   │           └─────────────────┘
// │USB │   └──────────┘             │                   │           ┌─────────────────┐
// │    │   ┌─────────┐  N_BatChg    │                   │◀━━━━━━━━━━┫     Buttons     │
// │    │   │ LTC4063 ├─────────────▶│                   │           └─────────────────┘
// │    ├─┬▶│ Charger │              │                   │           ┌──────────────────────────────┐
// │    │ │ │Regulator│   3.0V       │                   ├──────────▶│   Piezo Alarm/Servo (3.6V)   │
// │    │ │ │         ├──────▶       │                   │           └──────────────────────────────┘
// │    │ │ └────┬────┘              │                   │           ┌─────────────────────────────────┐
// └────┘ │      │                   │    ATMEGA328PB    │◀──────────┤ External Temperature/Analog In  │
//        │      │      3.6V         │                   │           └─────────────────────────────────┘
//        │      ├───────────▶       │                   │           ┌─────────────────────────────────┐
//        │    ──┴──                 │                   ├──────────▶│   High current MOSFET to GND    │
//        │     ─┬─  LiPO Cell       │                   │           └─────────────────────────────────┘
//        │      ▽                   │                   │  Reset    ┌─────────────────┐
//        │                          │                   ├──────────▶│  OLED Display   │
//        │USBVBus                   │                   │           └─────────────────┘
//        └─────────────────────────▶│                   │                     ▲
//                                   │                   │                     ┃
//                                   │                   │  I2C bus            ▼
//                                   │                   ┣━━━━━━━━━━━━━━━━━━━━━━━━━━━━━━━━━━━━━━━━━━━━━━━━━
//                                   └───────────────────┘  ▲             ▲               ▲              ▲
//                                                          ┃             ┃               ┃              ┃
//                                                          ▼             ▼               ▼              ▼
//                                                     ┌──────────┐  ┌──────────┐  ┌──────────────┐  ┌─────────┐
//                                                     │ Logging  │  │  BMP581  │  │   KX134ACR   │  │  QWIIC  │
//                                                     │  EEPROM  │  │ Pressure │  │ Accelerometer│  │Connector│
//                                                     │  256kB   │  │  Sensor  │  │              │  │         │
//                                                     └──────────┘  └──────────┘  └──────────────┘  └─────────┘
//
// Created with Monodraw
/*
            Five modes of operation are supported:
              FlightMode, BatteryChargeOnly, SerialHost, SealevelPressureSetMode, Set descent altitude for high current output
                1) Sea level Pressure Set Mode, using only the OLED and buttons to enter the sea level pressure.
                2) Flight mode, where we wait for lift off, log altitude, light, temperature with a thermistor on connector P3.
                3) Host connected serial utility mode, this will allow downloading of the EEPROM flight log, clearing the EEPROM, and setting the date-time.
                4) Battery charge mode, this will indicate charging for 5 seconds then turn off the OLED.
                5) Set the altitude for the high current output to be turned on.

                While in Flight mode, there are 5 flight phases:
                  1) Initialize
                  2) Wait for launch
                  3) Wait for apogee
                  4) Wait for landing
                  5) landed
                  6) Low power state

            If you are a developer, here is some helpful information
              Source code conventions:
                We use the prefix N_ for active low digital pins.
                Part way through the project we started adding a units suffix to variables to reduce unit confusion.
                Unused MCU pins must be either an output or an input with a pull up or down so the pins don't float and draw excess current.
              Programmer tips:
                1) This software keeps track of approximate date and time. This helps keep flight logs in order. Please keep the #define BIRTH_TIME_OF_THIS_VERSION up to date with every build.
                2) If you are adding software to Mia and need more FLASH space, you can:
                    A) Reduce or eliminate the instructions in DisplayInstructions() function. (Just comment out the call 'DisplayInstructions();', the linker will dead strip.)
                    B) Reduce or eliminate DoSplashScreen() function.
                    C) Reduce or eliminate DoSensorDisplayLoop() function as this is only used for diagnostics.
                    D) Reduce or eliminate the temperature look up table (about 412 bytes) and convert temperature differently, or not at all.
                    E) Remove auto-configuration support for the old Mia 0.0.0
                    F) Remove Buzzer function if not used.
                    G) Remove servo support if not used.
                    H) Revert to the standard ATMEGA328 Variant. You loose access to D23-D26 which may not matter but this saves a few hundred bytes.
                    I) Remove the host mode help command.
                    J) If a buzzer on-off pattern is not required, you can eliminate the DoBuzzer() function.
                3) Internaal EEPROM addresses 232 and up are unused.
                4) Test Point 7 has a hole on the board large enough to easily solder to, it is connected to D3. It is currently unused and available for any purpose.
                5) Many different sensors, Memory, controllers are available with a QWIIC connector that can be used with the Mia.

    @date   5/25/2025

    @note
    @verbatim
        Initial Board Bringup with a blank MCU:

          The first requirement is that you install minicore into the Arduino IDE so you can use the PB version of the ATMEGA328 that is on the Mia
            The Arduino bootloader doesn't support the new PB suffix part features.
            Go to https://github.com/MCUdude/MiniCore?tab=readme-ov-file#how-to-install and carefully follow the instructions.

          The second requirement is to have a bootloader programmer.
            In this example we use a Arduino Nano ESP32 as the programmer.
            To make a bootloader programmer you need a host Arduino that is 3.3 volts, a 5V Arduino will damage the pressure sensor and accelerometer.
            We use a Nano ESP32.
            Open the programmer with the ArduinoISP software, in File -> Examples -> 11.ArduinoISP -> ArduinoISP
            Uncomment the line:
            // #define USE_OLD_STYLE_WIRING
            It will be found in the area of lines 81 to 85 depending on your IDE version.

                  Setup the Arduino IDE:     Tools -> Board -> Arduino ESP32 boards ->Arduino Nano ESP32
                                             Tools -> Port ->  MACOS: similar to /dev/cu.usbserial34859F34317C7 (Arduino Nano ESP32)     Windows:

            Now click upload so ArduinoISP is programmed into your Arduino you are using as the programmer (Nano ESP32 in my case).
            The board you just programmed can be kept as a tool to re-program a bootloader that got corrupted.

          The third step is to program the bootloader into your Mia
                  Setup the Arduino IDE:     Tools -> Board -> MiniCore -> ATMEGA328.
                                             Tools -> Clock -> External 8 MHz
                                             Tools -> BOD -> BOD 1.8V      (Brown out detection voltage)
                                             Tools -> Variant -> 328PB
                                             Tools -> Port ->   MACOS: similar to /dev/cu.usbserial-DP05P0VC     Windows:
                                             Tools -> Programmer -> Arduino as ISP or Arduino as ISP (minicore)

            Now hook up your Mia as below

                     Mia to be programmed                                    
                              ┌──────┐                                       
                        ┌─────┤ USB  ├┐ ◀───  Do not hook up USB
                        │     │      ││                                      
                        │     └──────┘│                                      
                        │  ┌───┐      │                                      
                        │  │   │      │                                      
                        │  │P2 │      │                                      
                        │  │   │      │                                      
                        │  └───┘      │                                      
                        │             │                                      
                        │             │                                      
                        │             │                                      
                        │             │                                      
                        │             │                                      
                        │         O   │                    Programmer Board  
                        │   ┌─────┐   │                                      
                        │   │     │  O│◀───  -RESET         D10              
                        │   │ MCU │   │                                      
                        │   │     │  O│◀───  SCK            D13              
                        │   └─────┘   │                                      
                        │            O│◀───  MISO           D12              
                        │             │                                      
                        │            O│◀───  MOSI           D11              
                        │             │                                      
                        │            O│◀───  PLUS3.0V       3.3V             
                        │             │                                      
                        │            O│◀───  GND            GND              
                        │             │                                      
                        │       ┌──┐  │                                      
                        │       │  │  │                                      
                        │       │P1│  │                                      
                        │       │  │  │                                      
                        │ ┌──┐  └──┘  │                                      
                        │ │P4│        │                                      
                        │ └──┘┌───┐   │                                      
                        │     │   │   │                                      
                        │     │P3 │   │                                      
                        │     │   │   │                                      
                        │     │   │   │                                      
                        │     └───┘   │                                      
                        │        ┌┐   │                                      
                        │        ││   │                                      
                        │        ││   │                                      
                        │        ││   │                                      
                        └────────┴┴───┘                                      
            The programmer board powers your Mia. If programming fails, attach a battery to your Mia, turn the ON-OFF switch on, and re-try.
            Now, with your Mia attached to your Arduino programmer board, click Tools -> Burn Bootloader.
            Disconnect your Mia from the programmer.

          The Forth step is to upload Rocket_Altitude_4.6 into your Mia.
            Open Rocket_Altitude_4.6, or the latest version.
            Connect your Mia to your computer with the micro USB connector on the Mia
                      Setup the Arduino IDE: Tools -> Port ->   MACOS: similar to /dev/cu.usbserial-DP05P0VC or similar     Windows:
                        Verify these setting are as below:
                                             Tools -> Board -> MiniCore -> ATMEGA328.
                                             Tools -> Clock -> External 8 MHz
                                             Tools -> BOD -> BOD 1.8V      (Brown out detection voltage)
                                             Tools -> Variant -> 328PB
                                             Tools -> Programmer -> Arduino as ISP or Arduino as ISP (minicore)
            Click upload.
            NOTE: Important! Every time you update your Arduino IDE libraries you need to reset the minicore options above. An Arduino library update seems to reset those selection to some default and your upload will fail.

            After the upload is complete you should see the Mia startup message appear on the OLED. If you don't see anythin on the OLED, unplug the USB, turn the Mia off and re-seat your OLED in its connector. Then turn on again.




      MCU EEPROM Format:
            The MCU EEPROM format contains: <date>,<time>,<user>,<software info>,<sensors available><sensor specific block>
            The on chip EEPROM has a date and time field. These have no way of being current except for getting updated from a host computer
            It is not intended that these are accurate dates, but they are a source of "your data log was ON or AFTER this date"

            ADDR = 0: The time field is not a real time in any sense, but is incremented 10 seconds for each power cycle/flight. This allow the "time stamp" to keep logs in order
                and you know your data log was ON or AFTER the date in the log. After reset this field is check to be after the "born on" date, and a valid number.
                The format is a standard Linux signed time in seconds, but in 64 bit format. The Linux time 0 is midnight UTC on 1 January 1970. This should be as a "TAI" value.
                The EEPROM location supports 64 bits to avoid the year 2038 problem, but the software is not 64 bit ready.
                The Mia host application also updates this time to the current time.

            ADDR = 8: The last Known air pressure at sea level. This is a float.

            ADDR = 12: The next available address in the external EEPROM. uint32_t

            ADDR = 16: This field is a personalization field. The user can put any thing they want here but the intent is for name and contact information.
                This field is 63 characters long with the last byte as a end of string byte.   NOT INPLEMENTED

            ADDR = 80: This field is a software identification field. The software puts its name, version (from VersionString[]), and release date here.
                This field is up to 63 characters long with the last byte an end of string delimiter (\0).   NOT IMPLEMENTED

            ADDR = 144: The "feature available" field is 32 bits of enable bits for different features, sensors, or sensors with differnet setups.
                Bit  0  BMP390 pressure/temperature sensor
                Bit  1  Optical sensor with VEMT2523SLX01 and 1.00kΩ pull up resistor
                Bit  2  Memsic MC3416 Accelerometer
                Bit  3  Kionix KX134 Accelerometer
                Bit  4  1: 10 kΩ thermistor, muRata NXFT15XH103FEAB050, plugged in P3   0:Record voltage from P3
                Bit  5  BMP581 pressure/temperature sensor
                Bit  6  For output digital 9, SounderRequiresFrequency
                Bit  7  For output digital 9, 0=Servo output, 1=buzzer output

            ADDR = 148: The sensor specific block has the following:   NOT IMPLEMENTED
                (Should we put the BMP390/BMP581 sample rate, IIR filter coeff & oversampling stuff here? No, not yet.)

                ...
            ADDR = 160: 32 bytes. This 32 byte block is formatted exactly as a logging 32 byte record.
                The first 16 bit word is 0x0001 for its record number. The second 16 bit word is the status, fixed at 0x0100.
                The next 28 bytes are a string for latitude,longitude. Zero terminated allowing 27 bytes of location (including seperating comma). Set with "o" command.
                This is the last known launch location and will be included in the begininning of the next flight log. Format: <latitude>,<longitude>,0x00
                The host application will keep this updated if location services are available, if not, manual entry is available.

            ADDR = 192: Altitude setting for high current output. This is a float.

            ADDR = 196: Last maximum altitude reached in meters. This altitude is already be corrected for field altitude. This is a float.
                Read with "a" command.

            ADDR - 200: Servo position, pre-launch. This is a byte. Any value > 180 is invalid.
                Read and set with "p" command

            ADDR - 201: Servo position, ascent. This is a byte. Any value > 180 is invalid.
                Read and set with "p" command

            ADDR - 202: Servo position, at apogee. This is a byte. Any value > 180 is invalid.
                Read and set with "p" command
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
void loop() {


  readByteArray(EepromAddress, current_measurement.Bytes, 32);
  if (current_measurement.Record.RecordIndex == 0) {
    Serial.println("");
    Serial.println(F(" Addr   ,     Index,  ,        Status    ,   Mission Time,  ,     Altitude   ,   Temp     ,     Light/Sealevel,  ,    Linux Time-Date,  ,     X  ,      Y  ,      Z"));
  }
  SerialPrintHex(EepromAddress, 3);
  Serial.print(F(" , "));
  PrintRecord(current_measurement);
  Serial.println("");
  EepromAddress = EepromAddress + 32;
  //if (EepromAddress >= ExternalEEPROMSizeInBytes) {
  if (EepromAddress >= 262140) {
    while (1)
      ;
  }
}

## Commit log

2025-06-18 Host: unexpected unplug recovery, more reliable connection detection. Arduino: Added educational comments.
2025-06-23 Started fixing GUI for Raspberry Pi
2025-07-04 Added Wire.setWireTimeout to prevent lockup with damaged display.
2025-07-10 Mia: updates to landing detect. Comment cleanup. updates to altitude queue (not done)
2025-07-11 Mia: added servo sleep after low power mode. Host: better user status.
2025-07-11 Mia: fixed sample period for logging AND altitude queue
2025-07-12 Mia: Ver 4.6.23 fixed landing display
2025-07-13 Host: About window updates and Raspberry Pi fixes
2025-07-23 Fixed pressure calc from NWS data
2025-08-24 Mia:Rev.: 4.6.31 Fixed landing detection (was checking for difference when samples wern't updated due to sample period). Added summary record so we don't lose max altitude.
2025-10-04 rev 4.6.35 Corrected and added comments. Details added in sample period section and log format section at end. Made START_LOGGING_INTEGRATING_THRESHOLD more sensitive since we failed at launch detect.
2025-11-17 ver 4.6.39 fixed launch detect, fixed set date-time host command. landing detect has untested fix.
    [DiagnosticLogger.ino, External_EEPROM_Dump.ino]
2025-12-07 rev 4.6.47, Removed buggy abnormal termination detect and added an update to the end of logging MCU EEPROM address for every 200 samples instead. Fixed 'd' command end of flight log detect. Still hav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
2025-12-09 Mia Host - fixed bug updating sea level pressure on Mia
2025-12-11 ver 4.6.50, Speeded up logging EEPROM writes. we now collect records with 8 to 15 milliseconds between samples.
2025-12-19 Firmware: Sample rate improvements
2025-12-22 Firmware 4.6.54 This time I really did remove all the debug stuff. Changed Altitude threshold for high current output adjustment to 50ft. Changed flightModePhase1 to use less flash.
2025-12-27 Firmware Ver 4.6.55 & 4.6.56-Refactored pre-launch altitude/timestamp queue with circular buffer. Turned landing detection in to a more simple function. Removed diag prints.
2026-05-09 Switch from table to Steinhart-Hart Formula for temperature conversion
2026-05-26 fixed launch detect and landing detect yet again
2026-06-16 Ver 4.6.66 - Added simple newAltitude filter. Updated jolt detector. Speeded up instruction button response.
